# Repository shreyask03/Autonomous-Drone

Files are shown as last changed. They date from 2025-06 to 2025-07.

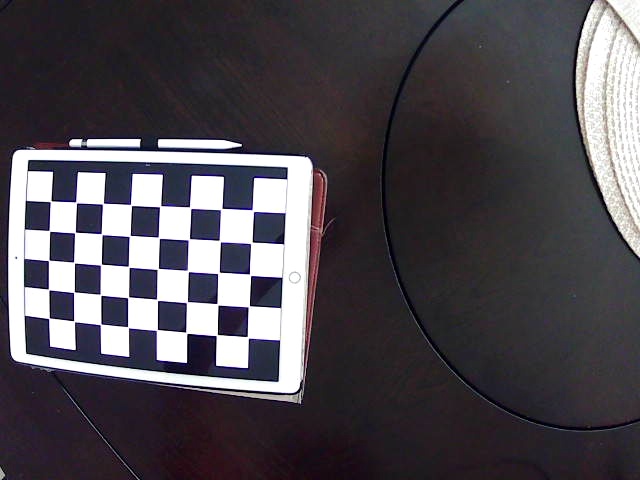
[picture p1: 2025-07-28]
calib_images/img_04.jpg

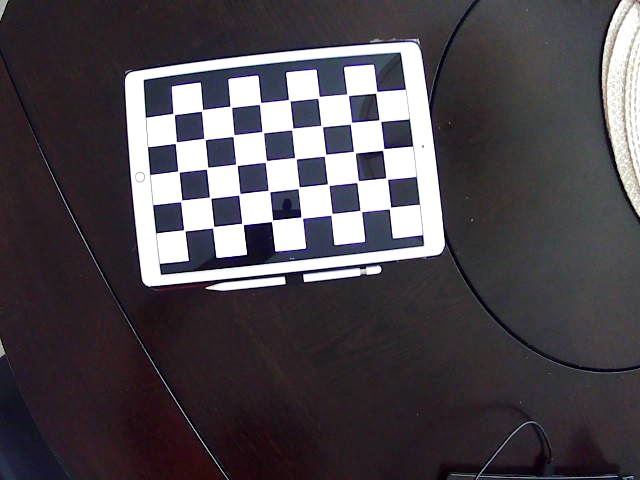
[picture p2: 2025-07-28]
calib_images/img_00.jpg

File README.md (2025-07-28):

# Explanations And Context About The Project

# Summary
This repository contains an Arduino based flight controller program for a drone with 4 propellers (quadrotor). 
It utilizes 3 axis PID feedback control architecture that has a cascaded structure. 
The lowest level of PID control takes as input a desired angular rotation rate and compares it to the measured rate 
from the onboard gyroscope to output motor speed corrections that reduce the difference in rates, the error, down to 0. This control loop operates at 250 Hz
for smooth resolution in control effort. The next level of control takes as input a desired angle and compares it to the measured angle 
from a filtered inertial measurement unit (IMU) output that combines both gyroscope and accelerometer data for smooth, noiseless readings.

# CAD Models
Furthermore, the repo also contains SOLIDWORKS parts/assembly of the drone frame, alongside .STEP214 files inside the CAD_Models folder 
that can be used to 3D print the same frame that I used. Keep in mind that this will be updated as I go, 
but I might leave older working frame iterations to make repairs easier or for people to get into the project from the beginning.

# WiFi Communication Setup Explanation
With that being said, after building and assembling the frame along with all electronic components, 
I ran into a frustrating issue that I have since resolved. For more context, it is essential that the drone's PID control system is tuned
properly, prior to being able to hold a successful flight test, because otherwise the drone will be completely uncontrollable and may crash
or worse, injure somebody. So I would suggest watching youtube videos on what each term in PID is doing, and how the tuning process looks to 
get an idea of what is going on before attempting anything yourself.

Basically, the standard way to tune the control system would be to plug the arduino in, change the initialized PID objects values, 
and then test it on a stand, rinsing and repeating until steady control is achieved. 
The problem lies here: There may be lots of fine tuning involved, and having to turn the drone off, connect it to the Arduino IDE, 
change the control gains, upload code, then test, is a pretty long process. Although not a problem when doing it a couple times.
I personally had to go back and forth countless times, and after a certain point I decided to implement a new system that would make things
far easier for me. I developed communication over WiFi using TCP or request based communication between the flight controller and my 
base station (a laptop in my case). I incorporated the communication through a custom graphical user interface (GUI) on the base station
to easily send tuning gains over once connected to the flight controller, and it shows the latest tune after a request is sent automatically
upon both opening the GUI as well as after sending a new tune over. This siginificantly shortened the time needed to tune and 
I was finally able to tune my drone and get things working properly.

Here ends the final stage for manual control using a radio.

# Beginning Drone Autonomy Development via ROS 2 Humble
After this point, I planned on making the drone fly autonomously using smart waypoint navigation. 
I realized what else I could do with the right sensors and ended up finding out about ROS.

From here, I've setup a ROS 2 Humble workspace on Ubuntu 22.04.5 LTS and have created a custom package for use
in simulations, as well as visualizations when I run LiDAR-based SLAM and visual SLAM in the near future from my base station
using publisher nodes set up on an onboard Raspberry Pi, acting as a sensor bridge. This allows me to reduce
computational load onboard the drone, therefore reducing the power consumption of an already power hungry Raspberry Pi
in order to squeeze out as much flight time as possible.

I plan on incorporating a method for simulating a 3D LiDAR scan using a 360 degree 2D LiDAR eventually to visualize
dense 3D reconstructions of the environments the drone flies through. 

# WILL UPDATE FROM HERE

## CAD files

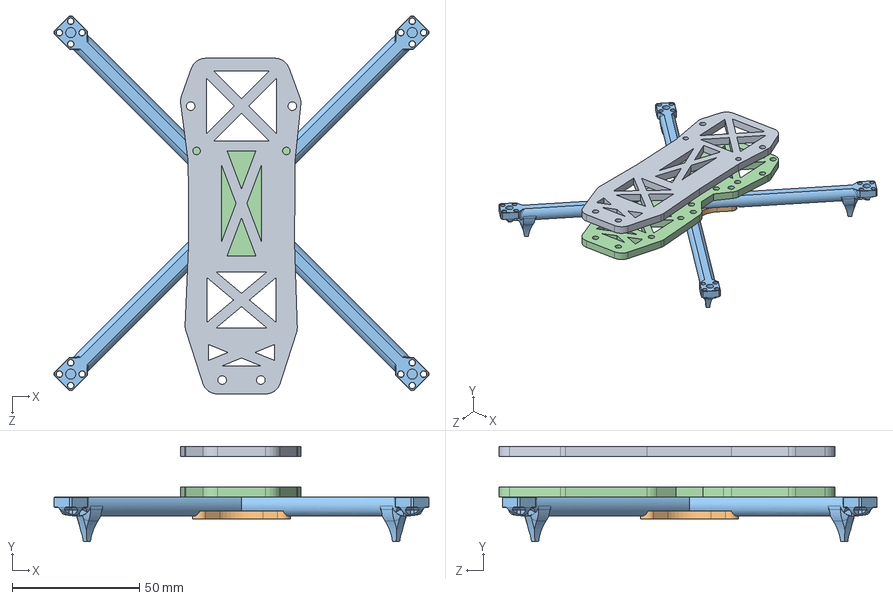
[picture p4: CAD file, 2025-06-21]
CAD Models/Autonomous_Drone/drone_frame_v1.SLDASM
147.4 x 37.5 x 148.7 mm
base_v1
3in_drone_arm_v1 x 4
arm_mounting_bracket
battery_tray_roof

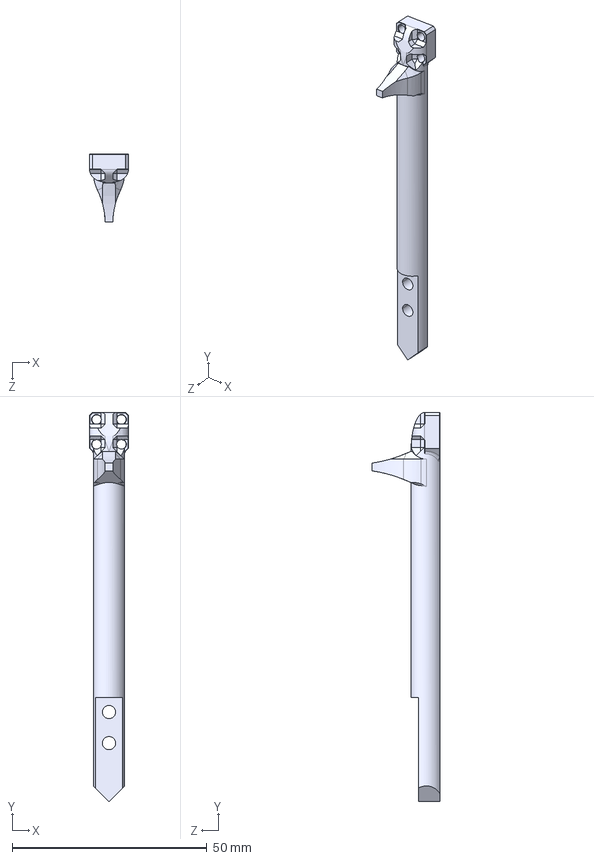
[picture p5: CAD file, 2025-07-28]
CAD Models/Autonomous_Drone/files to print/3in_drone_arm_v1.STEP
10.0 x 100.0 x 17.5 mm

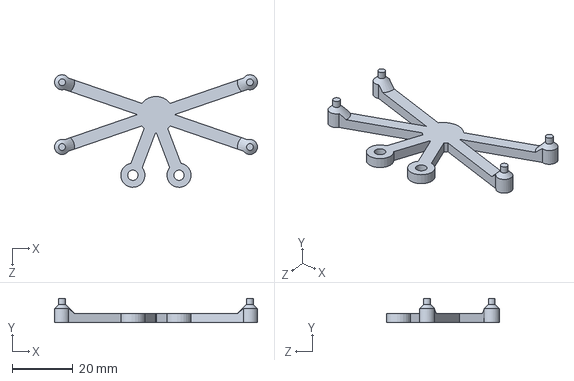
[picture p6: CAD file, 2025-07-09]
CAD Models/Autonomous_Drone/portenta_mount.SLDPRT
67.0 x 8.00 x 37.1 mm

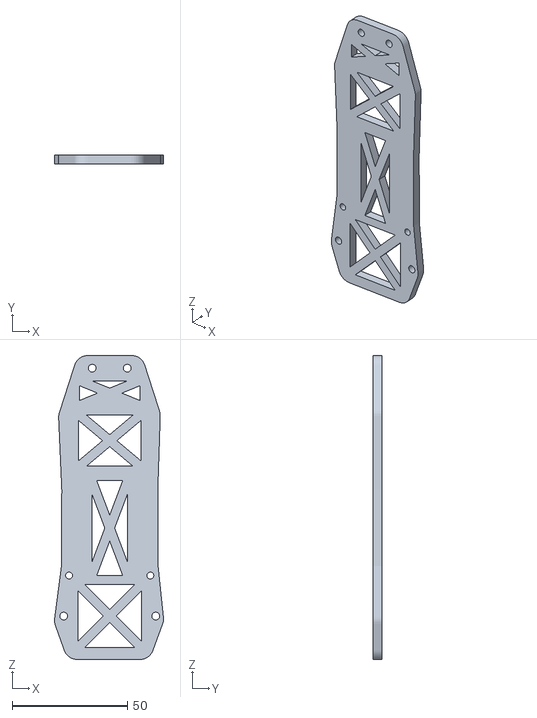
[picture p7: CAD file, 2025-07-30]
ros2_ws/src/drone/meshes/battery_tray_roof.STL
47.4 x 4.00 x 132.1

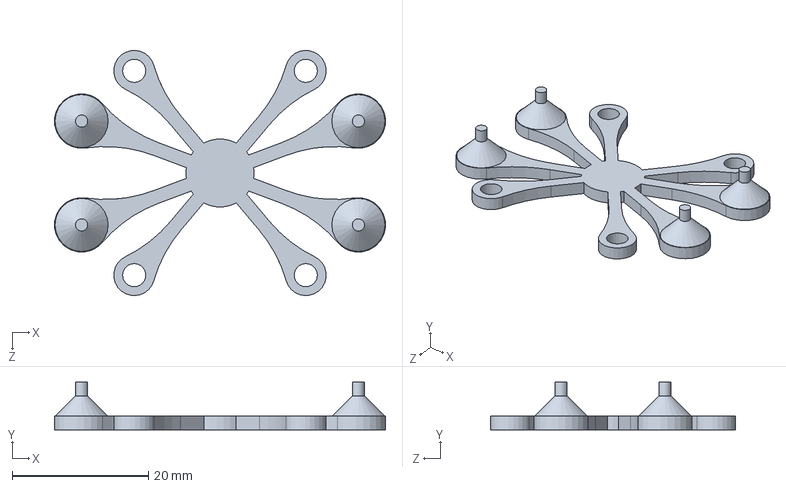
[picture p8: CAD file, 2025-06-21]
CAD Models/Autonomous_Drone/arduino_mount.SLDPRT
48.6 x 7.00 x 36.0 mm

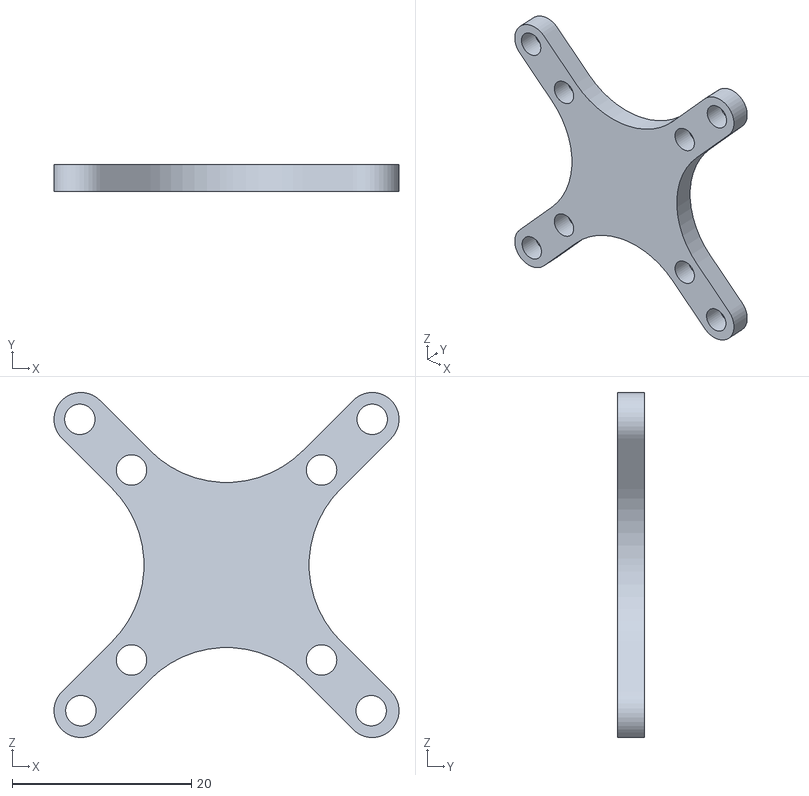
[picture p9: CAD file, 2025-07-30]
ros2_ws/src/drone/meshes/arm_mounting_bracket.STL
38.5 x 3.00 x 38.5

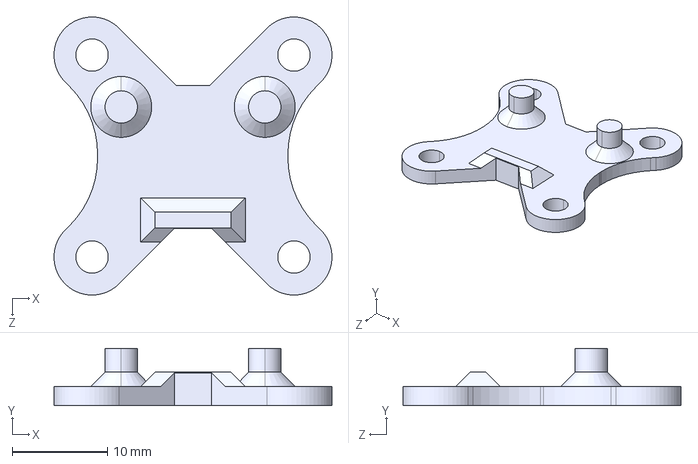
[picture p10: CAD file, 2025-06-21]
CAD Models/Autonomous_Drone/files to print/MPU_mount.STEP
29.2 x 6.00 x 29.2 mm

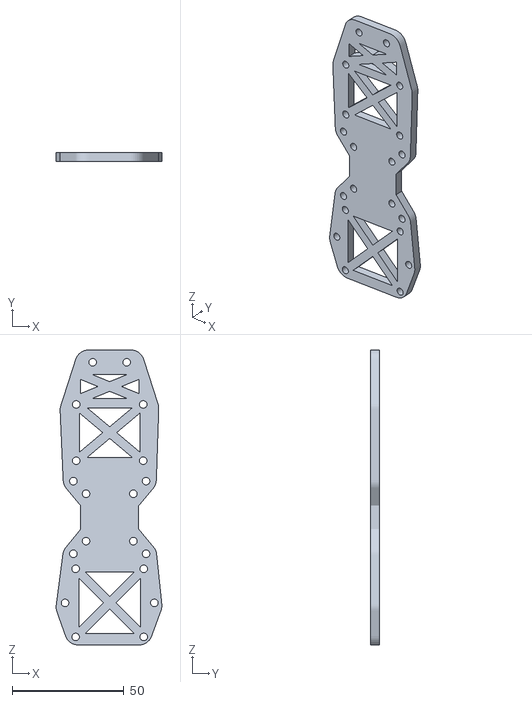
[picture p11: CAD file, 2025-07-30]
ros2_ws/src/drone/meshes/base_v1.STL
47.4 x 4.00 x 132.1

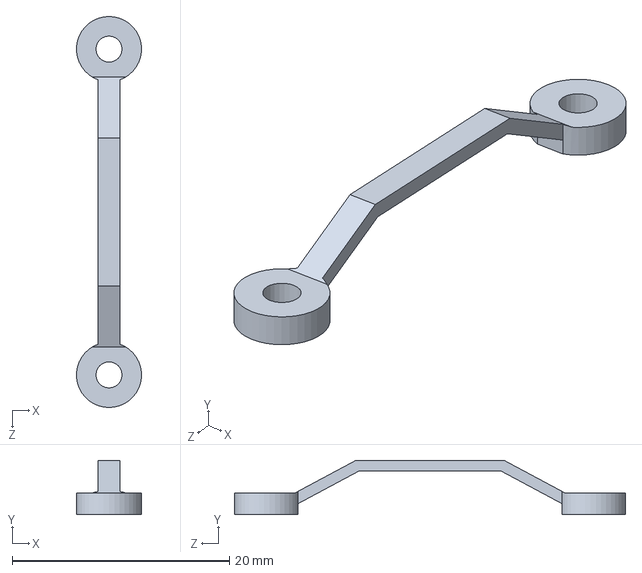
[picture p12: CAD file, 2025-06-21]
CAD Models/Autonomous_Drone/arduino_mount_lid.SLDPRT
5.98 x 5.00 x 36.0 mm

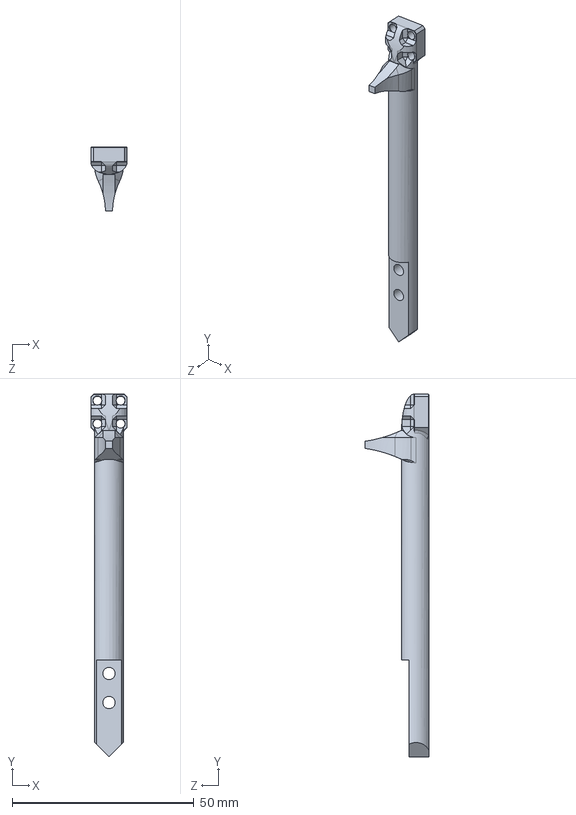
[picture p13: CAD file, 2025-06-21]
CAD Models/Autonomous_Drone/3in_drone_arm_v1.SLDPRT
10.0 x 100.0 x 17.5 mm

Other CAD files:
CAD Models/Autonomous_Drone/files to print/portenta_mount.STEP
CAD Models/Autonomous_Drone/arm_mounting_bracket.SLDPRT
CAD Models/Autonomous_Drone/files to print/arduino_mount.STEP
ros2_ws/src/drone/meshes/3in_drone_arm_v1.STL
CAD Models/Autonomous_Drone/battery_tray_roof.SLDPRT
CAD Models/Autonomous_Drone/files to print/arm_mounting_bracket.STEP
CAD Models/Autonomous_Drone/files to print/base_v1.STEP
CAD Models/Autonomous_Drone/base_v1.SLDPRT
CAD Models/Autonomous_Drone/MPU_mount.SLDPRT
CAD Models/Autonomous_Drone/files to print/battery_tray_roof.STEP

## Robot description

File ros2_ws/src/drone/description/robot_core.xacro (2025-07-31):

<?xml version="1.0"?>
<robot xmlns:xacro="http://www.ros.org/wiki/xacro">

    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
    <xacro:include filename="inertia_macros.xacro"/>

    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 
    <link name="base_link">
    </link>

    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
    <joint name="frame_joint" type="fixed">
        <parent link="base_link"/>
        <child link="frame_link"/>
        <origin xyz = "0 0 0.024"/>
    </joint>

    <link name="frame_link">
        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
        <xacro:box mass="0.306" x="0.13" y="0.045" z="0.02" origin_xyz="0 0 -0.01" origin_rpy="0 0 0"/>

    </link>

    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
    <joint name="fl_motor_joint" type="fixed">
        <parent link="base_link"/>
        <child link="fl_motor"/>
        <origin xyz="0.0707 0.0707 0" rpy="0 0 ${-pi/4 - pi/2}"/>
    </joint>

    <link name="fl_motor">
        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
        <xacro:cyl_end_x mass="0.016" r="0.004" l="0.1" origin_xyz="0.0211 0 0" origin_rpy="0 0 0"/>
        
    </link>

    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
    <joint name="fr_motor_joint" type="fixed">
        <parent link="base_link"/>
        <child link="fr_motor"/>
        <origin xyz="0.0707 -0.0707 0" rpy="0 0 ${pi/4 + pi/2}" />
    </joint>

    <link name="fr_motor">
        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
        <xacro:cyl_end_x mass="0.016" r="0.004" l="0.1" origin_xyz="0.0211 0 0" origin_rpy="0 0 0"/>

    </link>

    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
    <joint name="bl_motor_joint" type="fixed">
        <parent link="base_link"/>
        <child link="bl_motor"/>
        <origin xyz="-0.0707 0.0707 0" rpy="0 0 ${-pi/4}" />
    </joint>

    <link name="bl_motor">
        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
        <xacro:cyl_end_x mass="0.016" r="0.004" l="0.1" origin_xyz="0.0211 0 0" origin_rpy="0 0 0"/>

    </link>

    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
    <joint name="br_motor_joint" type="fixed">
        <parent link="base_link"/>
        <child link="br_motor"/>
        <origin xyz="-0.0707 -0.0707 0" rpy="0 0 ${pi/4}" />
    </joint>

    <link name="br_motor">
        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
        <xacro:cyl_end_x mass="0.016" r="0.004" l="0.1" origin_xyz="0.0211 0 0" origin_rpy="0 0 0"/>

    </link>

    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
    <joint name="fl_prop_joint" type="continuous">
        <parent link="fl_motor"/>
        <child link="fl_prop"/>
        <origin xyz="0 0 0.01" rpy="0 0 0"/>
        <axis xyz="0 0 1"/>
    </joint>

    <link name="fl_prop">
        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
        <xacro:cyl_center_z mass="0.003" r="0.038" l="0.004"/>

    </link>

    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
     <joint name="fr_prop_joint" type="continuous">
        <parent link="fr_motor"/>
        <child link="fr_prop"/>
        <origin xyz="0 0 0.01" rpy="0 0 0"/>
        <axis xyz="0 0 -1"/>
    </joint>

    <link name="fr_prop">
        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
        <xacro:cyl_center_z mass="0.003" r="0.038" l="0.004"/>

    </link>

    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
     <joint name="bl_prop_joint" type="continuous">
        <parent link="bl_motor"/>
        <child link="bl_prop"/>
        <origin xyz="0 0 0.01" rpy="0 0 0"/>
        <axis xyz="0 0 -1"/>
    </joint>

    <link name="bl_prop">
        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
        <xacro:cyl_center_z mass="0.003" r="0.038" l="0.004"/>

    </link>

    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
     <joint name="br_prop_joint" type="continuous">
        <parent link="br_motor"/>
        <child link="br_prop"/>
        <origin xyz="0 0 0.01" rpy="0 0 0"/>
        <axis xyz="0 0 1"/>
    </joint>

    <link name="br_prop">
        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
        <xacro:cyl_center_z mass="0.003" r="0.038" l="0.004"/>

    </link>

    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

</robot>

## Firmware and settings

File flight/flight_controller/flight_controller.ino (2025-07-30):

#include "receiver.h"
#include "motor.h"
#include "mpu.h"
#include "pid.h"
#include "comms.h"

//initialize sensors and motors
Receiver rx;

Motor FL(11); // front left
Motor FR(3); // front right
Motor BL(10); // back left
Motor BR(9); // back right

MPU mpu;

static constexpr int RATE_LIMIT = 150; // deg/s
static constexpr int ANGLE_LIMIT = 30; // deg

// initialize PID axes for rate control
PID roll(0.6,1.5,0.08);
PID pitch(0.75,1.5,0.08);
PID yaw(1,1.5,0.005);

// initialize new PID objects for angle control
PID rollAngle(2.75,0.2,0.2,RATE_LIMIT);
PID pitchAngle(3.25,0.2,0.2,RATE_LIMIT);

// initialize communication object
Comms comms(&pitch,&roll,&yaw,&pitchAngle,&rollAngle,&rx);

//initialize control loop variables
int throttle;

float desiredRoll;
float desiredPitch;
float desiredYaw;

float desiredRollRate;
float desiredPitchRate;

float currRollRate;
float currPitchRate;
float currYawRate;

float rollContribution;
float pitchContribution;
float yawContribution;

// Global variables for loop timing purposes
unsigned long prev_acro_loop = 0;
unsigned long prev_angle_loop = 0;
const unsigned long ACRO_PERIOD = 4000; // microsecond value locks 250 hz loop rate
const unsigned long ANGLE_PERIOD = 10000; // microsecond value locks 100 hz loop rate (angle mode)


ISR(PCINT0_vect){
  rx.handleInterrupt();
}

void setup() {
  // put your setup code here, to run once:
  // debugging use
  // Serial.begin(115200);

  // initialize receiver
  rx.init();

  // wait for rx and tx to establish connection
  rx.waitForConnect();

  // now safe to initialize motors
  FL.init();
  FR.init();
  BL.init();
  BR.init();

  // initialize mpu
  mpu.init();

  // reset PID values
  roll.reset();
  pitch.reset();
  yaw.reset();
  pitchAngle.reset();
  rollAngle.reset();
  comms.init();
  
}

void loop() {

  unsigned long now = micros(); // loop timer variable

  if(!rx.isArmed()){
    // shut motors off
    FL.write(1000); // 1ms pulse = 0% throttle
    FR.write(1000);
    BL.write(1000);
    BR.write(1000);
    // reset PID values
    roll.reset();
    pitch.reset();
    yaw.reset();
    pitchAngle.reset();
    rollAngle.reset();

    rx.waitForConnect();

    static String serialInput = "";
    char buffer[100];  // <-- declare buffer here

    while (Serial.available()) {
      char c = Serial.read();
      if (c == '\n') {
        serialInput.trim();
        if (serialInput.length() > 0) {
          serialInput.toCharArray(buffer, sizeof(buffer));
          comms.parseMessage(buffer);
        }
        serialInput = "";
      } else {
        serialInput += c;
      }
    }
  }
  else{

    /* ANGLE MODE - 100 hz
        ACRO MODE - 250 hz*/

    // ANGLE MODE
    if(rx.isAngle()){

      // calculate desired rates at 100hz 
      if(now - prev_angle_loop >= ANGLE_PERIOD){
        prev_angle_loop += ANGLE_PERIOD;

        // get pilot inputs
        throttle = rx.getThrottle();
        desiredRoll = rx.getAngle(1,ANGLE_LIMIT);
        desiredPitch = rx.getAngle(2,ANGLE_LIMIT);
        desiredYaw = rx.getRate(4, RATE_LIMIT);

        mpu.updateGyro();
        mpu.updateAccel();
        MPU::Vector3 angles = mpu.computeAngles();

        float currRollAngle = angles.x;
        float currPitchAngle = angles.y;

        MPU::Vector3 rates = mpu.getGyro();
        currYawRate = rates.z;

        // compute desired rates from angle PID loops
        desiredRollRate = rollAngle.compute(desiredRoll, currRollAngle);
        desiredPitchRate = pitchAngle.compute(desiredPitch, currPitchAngle);
        // desired yaw is handled in rate mode

      }

      // inner rate loop at 250hz
      if(now - prev_acro_loop >= ACRO_PERIOD){
        prev_acro_loop += ACRO_PERIOD;

        throttle = rx.getThrottle(); // keep throttle updated at 250hz

        if(throttle >= 1100){
          // read gyro rates
          mpu.updateGyro();
          MPU::Vector3 rates = mpu.getGyro();

          currRollRate = rates.x;
          currPitchRate = rates.y;
          currYawRate = rates.z;

          // compute PID outputs for each axis
          rollContribution = roll.compute(desiredRollRate,currRollRate);
          pitchContribution = pitch.compute(desiredPitchRate,currPitchRate);
          yawContribution = yaw.compute(desiredYaw,currYawRate);
        } else{
          rollContribution = 0;
          pitchContribution = 0;
          yawContribution = 0;
          roll.reset();
          pitch.reset();
          yaw.reset();
          rollAngle.reset();
          pitchAngle.reset();
        }

        // mix motor channels (i.e. add PID corrections to throttle)
        int base_throttle = throttle; // copy throttle to issues with overwriting or tearing with value being read in

        // Sign convention: pitch forward(front down) is positive, roll right(right down) is positive, yaw right(clockwise viewed from top) is positive
        int pulse_FL = constrain(base_throttle - pitchContribution + rollContribution - yawContribution,1000,2000);
        int pulse_FR = constrain(base_throttle - pitchContribution - rollContribution + yawContribution,1000,2000);
        int pulse_BL = constrain(base_throttle + pitchContribution + rollContribution + yawContribution,1000,2000);
        int pulse_BR = constrain(base_throttle + pitchContribution - rollContribution - yawContribution,1000,2000);


        // write to motors
        FL.write(pulse_FL);
        FR.write(pulse_FR);
        BL.write(pulse_BL);
        BR.write(pulse_BR);

      }

    }

    // ACRO MODE (RATE LOOP ONLY)
    else{

      if(now - prev_acro_loop >= ACRO_PERIOD){
        prev_acro_loop += ACRO_PERIOD;

        // get pilot inputs
        throttle = rx.getThrottle();
        desiredRoll = rx.getRate(1, RATE_LIMIT);
        desiredPitch = rx.getRate(2, RATE_LIMIT);
        desiredYaw = rx.getRate(4, RATE_LIMIT);

        if(throttle >= 1100){
          // get current rates
          mpu.updateGyro();
          MPU::Vector3 rates = mpu.getGyro();

          currRollRate = rates.x;
          currPitchRate = rates.y;
          currYawRate = rates.z;

          // calculate PID contributions
          rollContribution = roll.compute(desiredRoll,currRollRate);
          pitchContribution = pitch.compute(desiredPitch,currPitchRate);
          yawContribution = yaw.compute(desiredYaw, currYawRate);

        } else{
          rollContribution = 0;
          pitchContribution = 0;
          yawContribution = 0;
          roll.reset();
          pitch.reset();
          yaw.reset();
        }

        // mix motor channels (i.e. add PID corrections to throttle)
        int base_throttle = throttle; // copy throttle to issues with overwriting or tearing with value being read in

        // Sign convention: pitch forward(front down) is positive, roll right(right down) is positive, yaw right(clockwise viewed from top) is positive
        int pulse_FL = constrain(base_throttle - pitchContribution + rollContribution - yawContribution,1000,2000);
        int pulse_FR = constrain(base_throttle - pitchContribution - rollContribution + yawContribution,1000,2000);
        int pulse_BL = constrain(base_throttle + pitchContribution + rollContribution + yawContribution,1000,2000);
        int pulse_BR = constrain(base_throttle + pitchContribution - rollContribution - yawContribution,1000,2000);


        // write to motors
        FL.write(pulse_FL);
        FR.write(pulse_FR);
        BL.write(pulse_BL);
        BR.write(pulse_BR);
        
      }
    }
  }
}

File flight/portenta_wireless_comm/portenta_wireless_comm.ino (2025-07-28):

#include <WiFi.h>
#include "statusLED.h"


const char* ssid = "wifi_name";
const char* password = "wifi_pass";

const char* serverIP = "your_local_ip";
const uint16_t serverPort = 8000;

WiFiClient client;
statusLED s;

String lastReceived = "";
static constexpr int TIMEOUT = 5000; // ms
unsigned long lastConnectionCheck = 0;

void connectToWiFi() {
  s.connectingWiFi();
  WiFi.begin(ssid, password);

  int attempts = 5;
  while (WiFi.status() != WL_CONNECTED && attempts-- > 0) {
    delay(100);
  }
}

void connectToServer() {
  s.connectingServer();
  // Try multiple times to connect
  int retries = 5;
  while (!client.connect(serverIP, serverPort) && retries-- > 0) {
    delay(100);
  }
}

void setup() {
  s.init(); // initialize led pins
  // while(!Serial) delay(500);
  connectToWiFi();
  connectToServer();
  Serial1.begin(115200);
  Serial.begin(115200);
}

void loop() {
  // Serial.println("Loop Running"); // checks if loop is not getting stuck, if working properly should print every loop
  // Reconnect WiFi if dropped
  if (WiFi.status() != WL_CONNECTED) {
    connectToWiFi();
    return;
  }

  // Reconnect to server if dropped
  if (!client.connected()) {
    // Serial.println("Client disconnected! Retrying...");
    connectToServer();
    // Serial.println("Reconnected!");
    return;
  }

  // read data from server and process commands
  static String inputBuffer = "";
  while (client.available()) {
    char c = client.read();
    if (c == '\n') { // end of message reached
      inputBuffer.trim();
      if (inputBuffer.length() > 0) {
        if (inputBuffer == "REQUEST,TUNE") {
          client.print("ACK\n"); // send ACK immediately to server
          delay(10);
          client.flush();


          Serial1.println(inputBuffer); // Ask Nano for current tune
          String message = waitForSerial1Message();
          if (message.startsWith("TUNE")) {

            // client.print("ACK\n"); //send ACK to server first acknowledge successful read from nano
            // delay(10);
            // client.flush();

            client.print(message + '\n');
            client.flush(); // just to avoid any issues
            waitForAck(); // wait for ACK from server
          }
        }
        else if (inputBuffer.startsWith("TUNE")) {

          client.print("ACK\n"); // send ACK immediately to server
          delay(10);
          client.flush();

          Serial1.println(inputBuffer); // Send new tune to Nano
          String message = waitForSerial1Message();
          if (message.startsWith("TUNE")) {

            // client.print("ACK\n"); // send ACK to server
            // delay(10);
            // client.flush();

            client.print(message + '\n');
            client.flush();
            waitForAck(); // wait for ACK from server
          }
        }
      }
      inputBuffer = "";
    } else {
      inputBuffer += c;
    }
  }

  // Check for dead connection (no activity for > timeout)
  if (millis() - lastConnectionCheck > TIMEOUT) {
    if (!client.connected()) {
      connectToServer();
    }
    lastConnectionCheck = millis();
  }
}


void waitForAck(){
  s.dataTransfer();
  unsigned long startTime = millis();

  while(millis() - startTime < TIMEOUT){
    if(client.available()){
      String response = client.readStringUntil('\n');
      response.trim();
      if(response == "ACK"){
        return;
      }
    }
  }
}

String waitForSerial1Message() {
  unsigned long start = millis();
  String msg = "";
  while (millis() - start < TIMEOUT) {
    while (Serial1.available()) {
      char c = Serial1.read();
      if (c == '\n') {
        msg.trim();
        return msg;
      }
      msg += c;
    }
  }
  return ""; // Timeout or bad message
}

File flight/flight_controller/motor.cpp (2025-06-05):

#include "motor.h"

Motor::Motor(uint8_t motorPin) : pin(motorPin) {}

void Motor::init(){
  // configure pins as output
  pinMode(this->pin, OUTPUT);
}

void Motor::write(int pulse){
  /* create valid duty cycle value (% time on vs total period) as a fraction of 255 (8 bit max)
   - servos and esc input utilizes 1ms - 2ms pulse width duration
   - for ~ 490 Hz (488) the period is ~2.04 ms
   - duty cycle for 1ms (0% throttle) is 1/2.04 which is 49%, and for 2ms duty cycle is 98%
   - analogWrite requires integer from 0 to 255 (8 bit) which will represent duty cycle of pwm output
   - so 1-2ms pulse width durations correspond to an integer value between 125 (49% of 255) and 250 (98% of 255)*/
  int val = map(pulse,1000,2000,125,250); // map throttle to 8 bit value such that analogwrite can send a valid signal
  analogWrite(this->pin,val); // send pulse
}

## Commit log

2025-06-05 Initial Commit, working gyro mode
2025-06-05 renamed latest working code to avoid confusion
    [motor.cpp, mpu.cpp, receiver.cpp]
2025-06-05 added flight mode switch, rx signal debug function
2025-06-06 combined 3 axis raw gyro data conversion into 1 function
2025-06-06 fixed working gyro mode, copied incorrect version prior to repo setup
2025-06-08 functioning gyro mode with simplified mpu class
2025-06-12 added third party software folder currently include mpu6050 code
2025-06-21 Organized root directory, removed expired code
    [3in_drone_arm_v1.SLDPRT, 3in_drone_arm_v1.STEP, MPU_mount.SLDPRT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]
2025-07-09 fixed merge conflicts and updated feature branch with latest code for reworking
    [portenta_mount.SLDPRT, portenta_mount.STEP]
2025-07-28 successful flight test, completed angle mode, merging all changes to master to complete this portion of project.
    [3in_drone_arm_v1.STEP]
2025-07-28 Included rplidar_ros package for Slamtec RPLiDAR C1 sensor usage
2025-07-30 configured package for visualization in rviz
    [robot.urdf.xacro, robot_core.xacro]
2025-07-30 cleaned up flight/ codebase, added meshes into ros drone package
    [3in_drone_arm_v1.STL, arm_mounting_bracket.STL, base_v1.STL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]
2025-07-31 completed core drone model, added inertial macros, saved rviz2 drone frame viewer
    [inertia_macros.xacro, robot_core.xacro]
2025-07-31 Created simulated lidar sensor, created test gazebo world for simulation
    [lidar.xacro, robot.urdf.xacro, robot_core.xacro]
